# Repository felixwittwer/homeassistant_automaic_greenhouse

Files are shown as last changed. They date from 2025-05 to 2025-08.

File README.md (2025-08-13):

 &nbsp; &nbsp; 



<br>
<p align="center">
    
</p>
<br>

# homeassistant_automaic_greenhouse
A cool Project to make your greenhouse smart. What about automaic irrigation and collecting enviromental data right from your garden.

<p align="center">
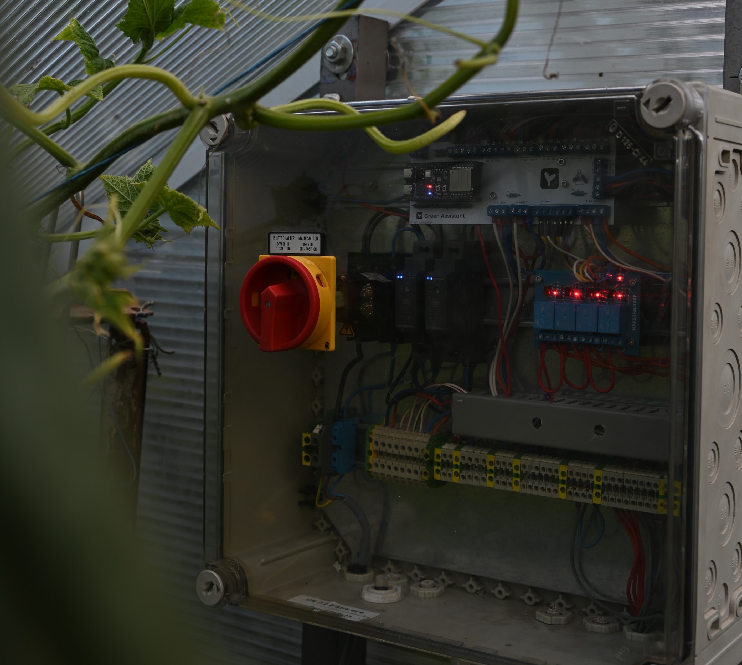
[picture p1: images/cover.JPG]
  
</p>

## About the project
This project actually is sthe second iteration on me trying to automate our greenhouse. The first version relied on an Arduino Uno powered by a 24V powertool battery and sensordata was logged to an SD-card. Since we now have power and wifi connectivity to the greenhouse I wanted to step up the game and build something that is way smarter and will hopefully last forever. If you were wondering this is why an industrial grade electrical box with rails was used.

## The concept of sensor and action modules
This project is a very specked out version of a greenhouse automation and environmental monitoring system. Due to cost or other reasons you might not include all the sensors used by me. To make it easyer to do so each sensor is getting his own folder inside the sensor modules directory. You will find everything you need to know about a so called sensor module inside this folder from CAD files, STL Files for 3D printing and scematics to instructions on sourcing the parts.

A detailed list of all sensors used in the project can be found in the [**sensor modules**](/sensor%20modules/) directory.

Like the sensors you might choose to leave out some action modules aka the parts that actually do something like the relais and solanoids for an irrigation system.

These so called action modules with all their corresponding documentation and files can be found in the [**action modules**](/action%20modules/) directory.

## Where to start

If you are completly new to this project you might take a look at the folowing map. Go thrugh the individual questions and build your own Green Assistant. Follow the link below to get to an interactive pdf version. Clicking on the links will be more func than searching in this Repo.

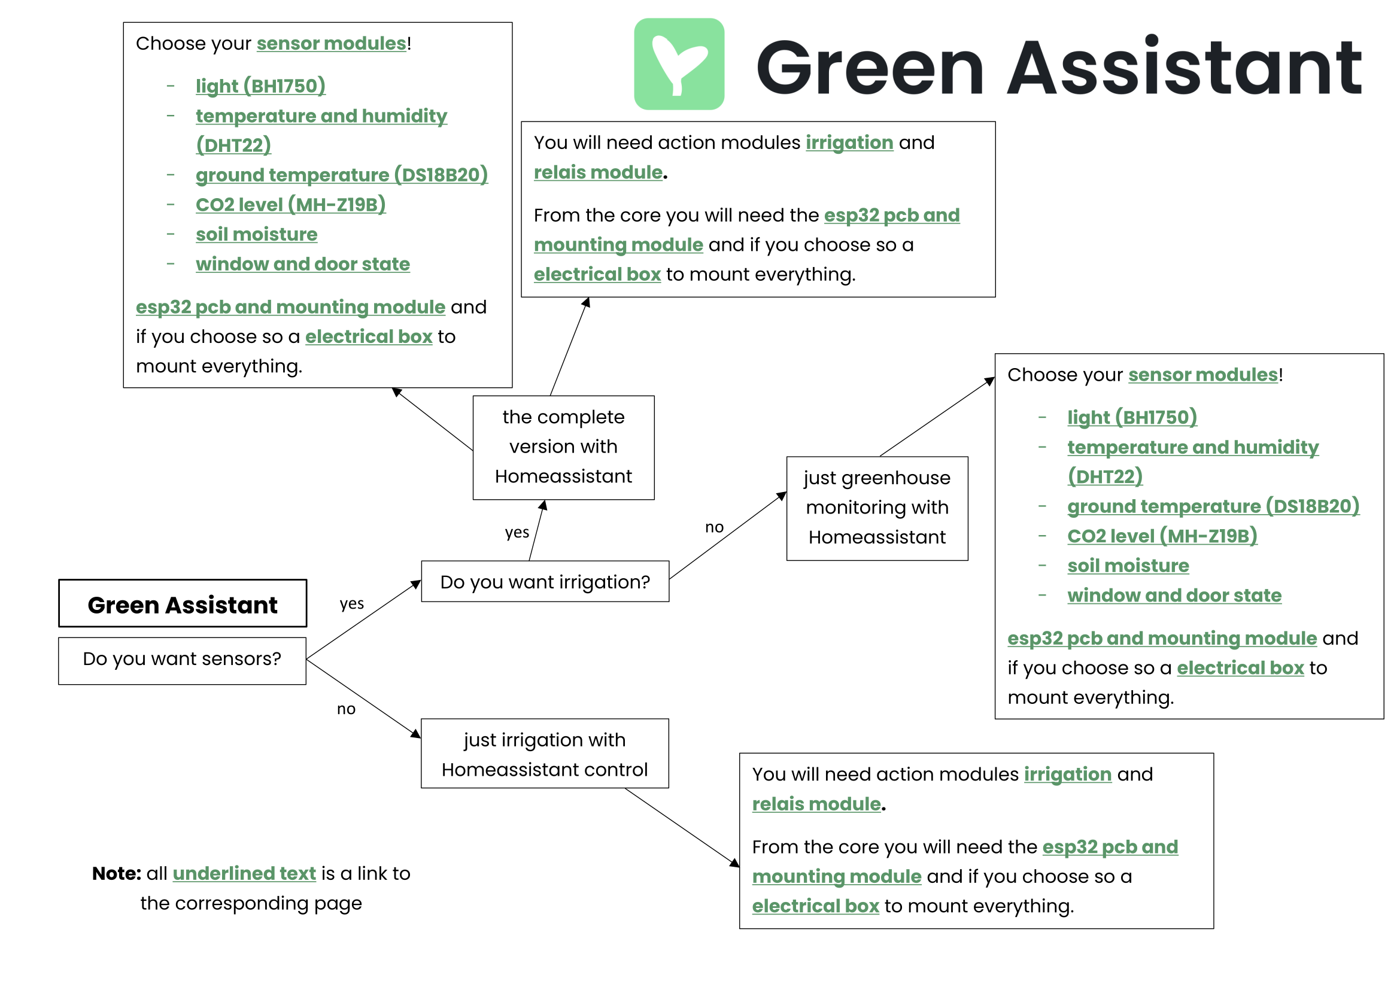
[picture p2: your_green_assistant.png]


<!-- ![Interactive PDF version](./your_green_assistant.pdf) -->

## The project

A list of all uesd parts can be found in the **parts** directory.

All files corresponding to the main part of the project so the electrical box with all the controll electronics can be found in the **core** directory.

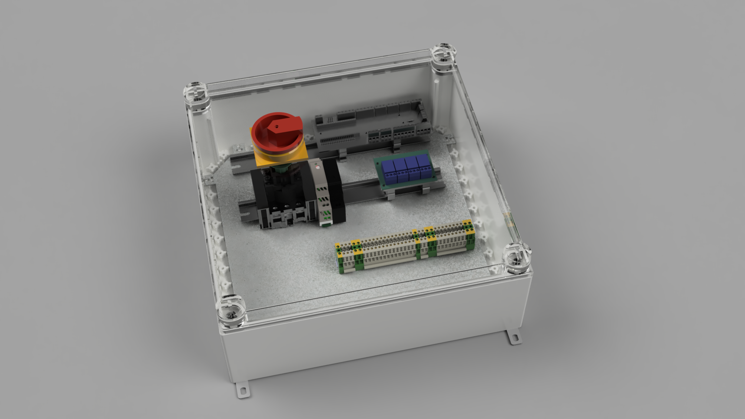
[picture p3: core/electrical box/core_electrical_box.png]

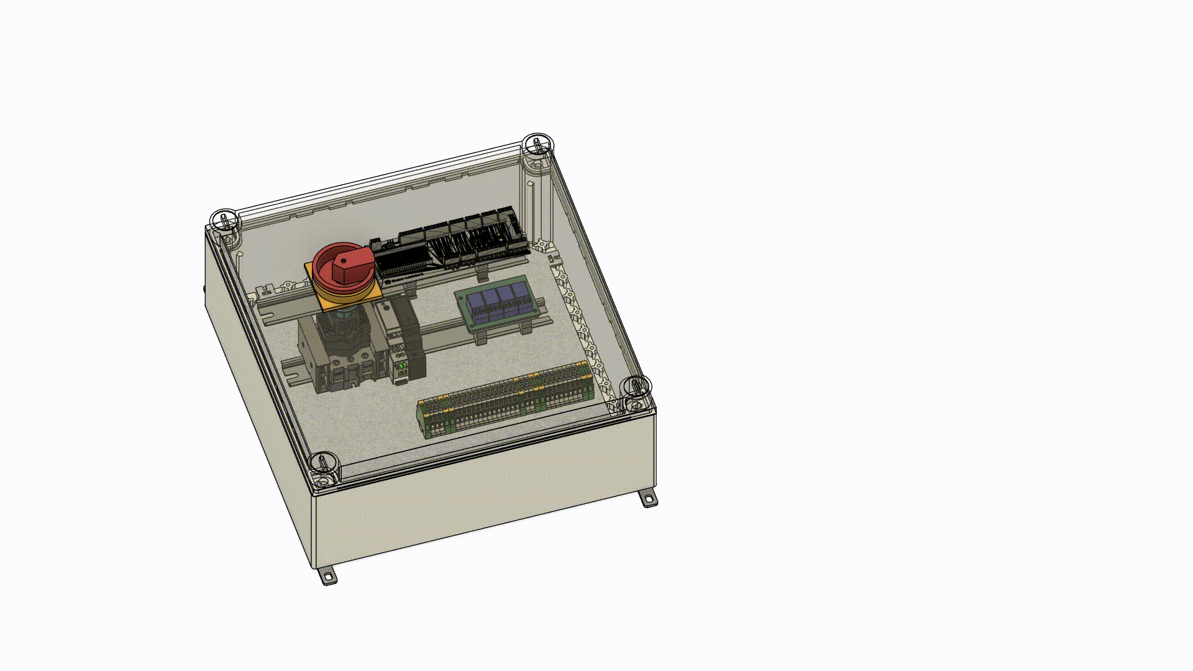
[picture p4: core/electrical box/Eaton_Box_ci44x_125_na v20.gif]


### Mounting hardware

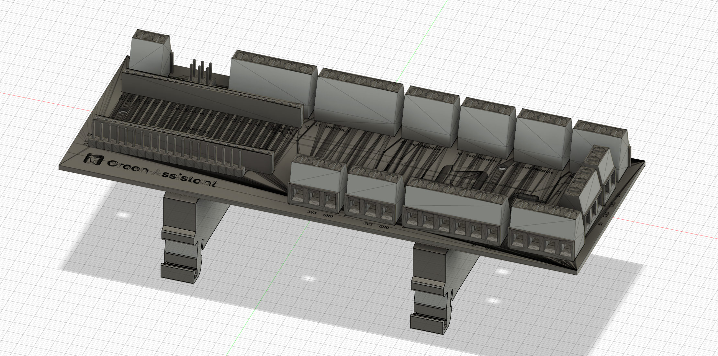
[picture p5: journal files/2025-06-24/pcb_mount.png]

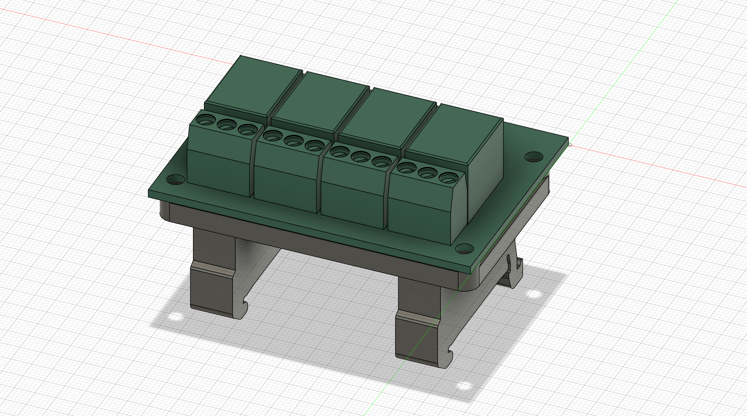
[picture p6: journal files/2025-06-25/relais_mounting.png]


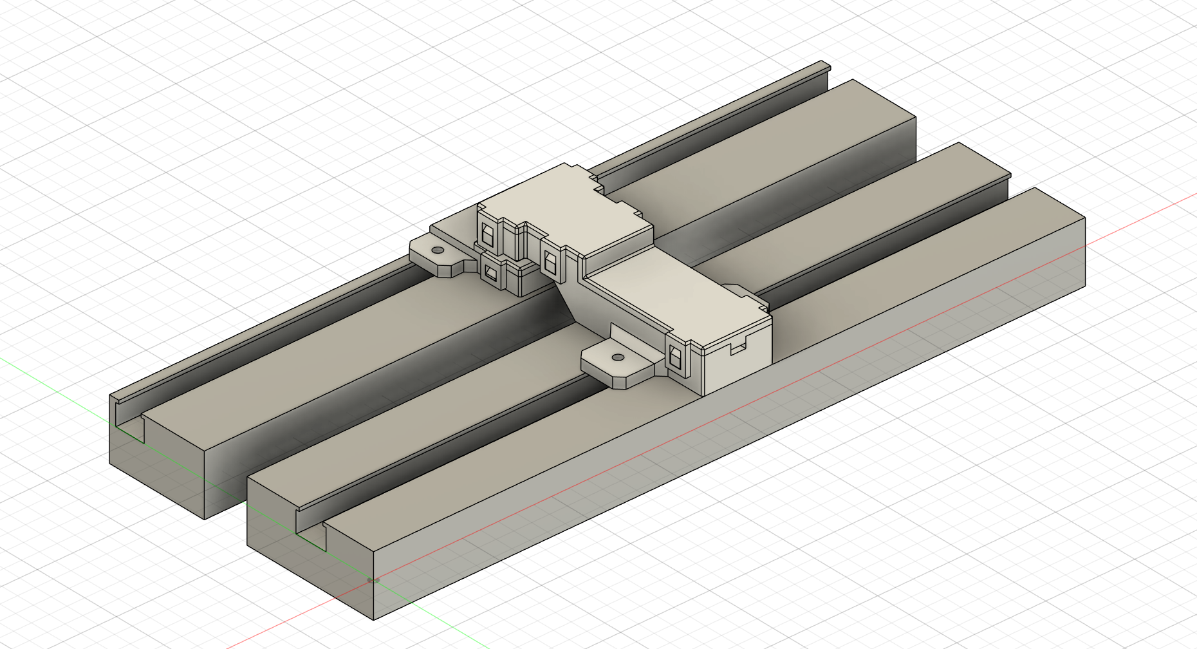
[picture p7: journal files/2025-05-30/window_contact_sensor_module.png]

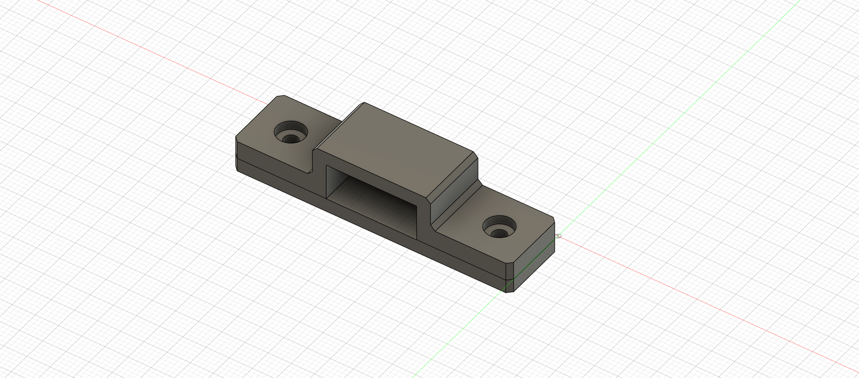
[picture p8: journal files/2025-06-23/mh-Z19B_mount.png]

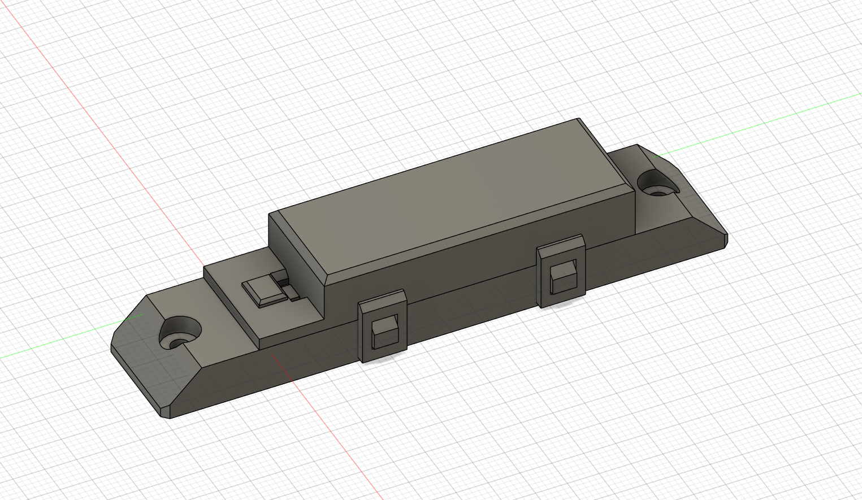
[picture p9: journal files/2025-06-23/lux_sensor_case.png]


### Irrigation system

<p float="left">
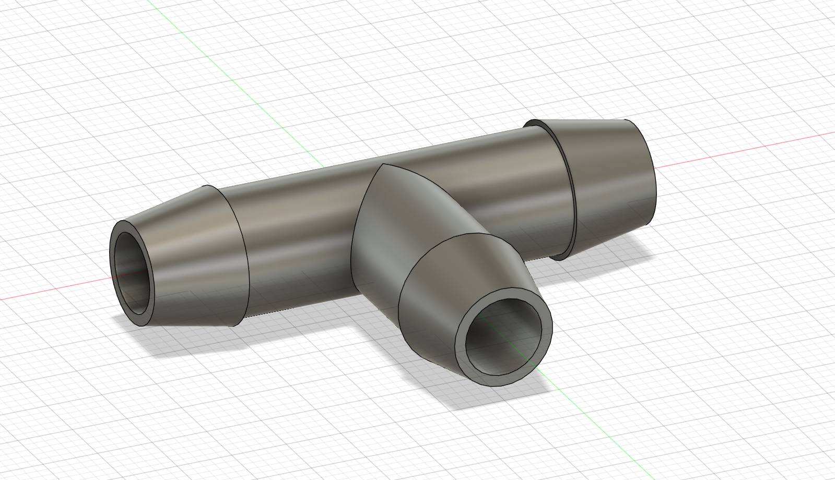
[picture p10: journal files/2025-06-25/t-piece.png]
  
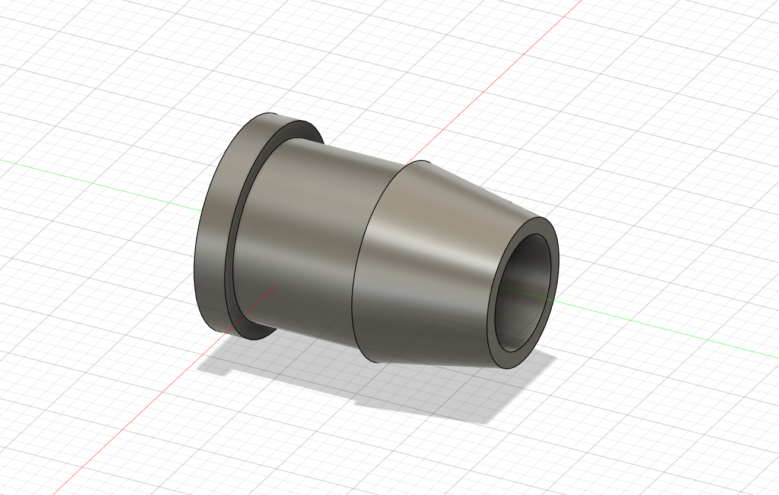
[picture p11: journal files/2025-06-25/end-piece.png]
  
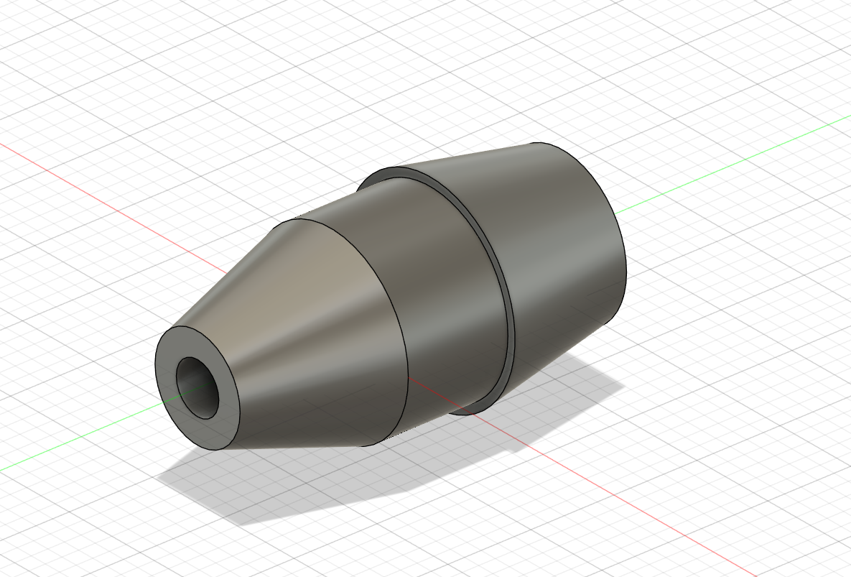
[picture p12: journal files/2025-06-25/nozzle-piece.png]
  
</p>

### PCB

You will need this PCB to connect all sensors reliably to the ESP32 S3. All unused pins of the ESP also have a connection to a pinheader so feel free to add sensors without needing to modify the PCB. 

PCB Sourcefiles can be found inside [core/esp32 pcb and mounting/pcb files/esp shield](./core/esp32%20pcb%20and%20mounting/pcb%20files/esp_shield/).

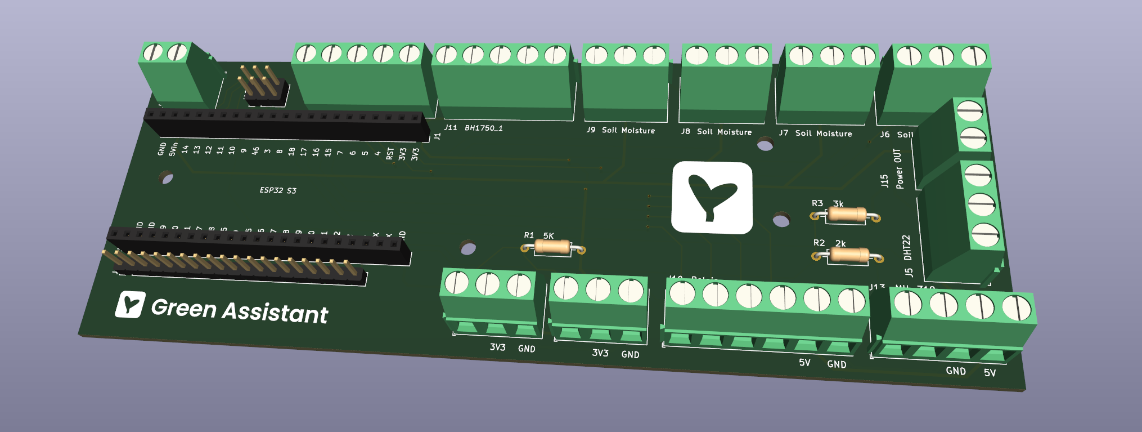
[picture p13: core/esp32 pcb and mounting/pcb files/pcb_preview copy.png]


<p float="left">
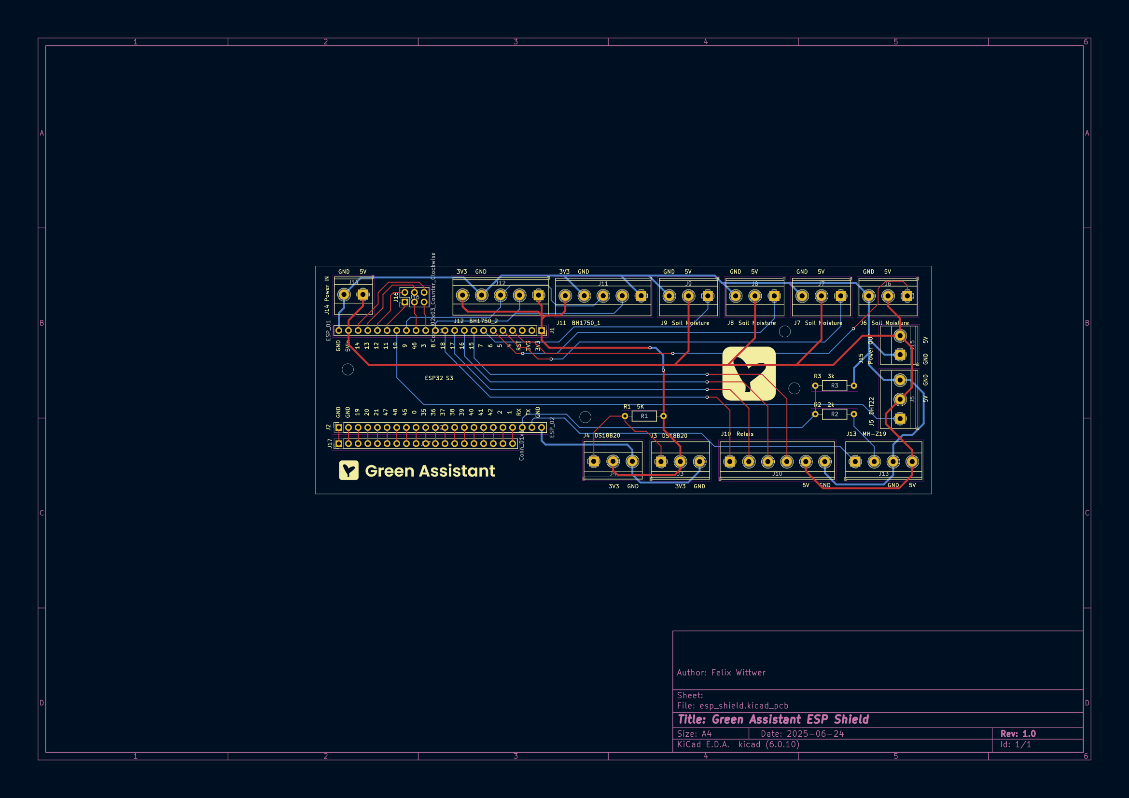
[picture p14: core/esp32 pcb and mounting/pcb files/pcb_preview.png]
  
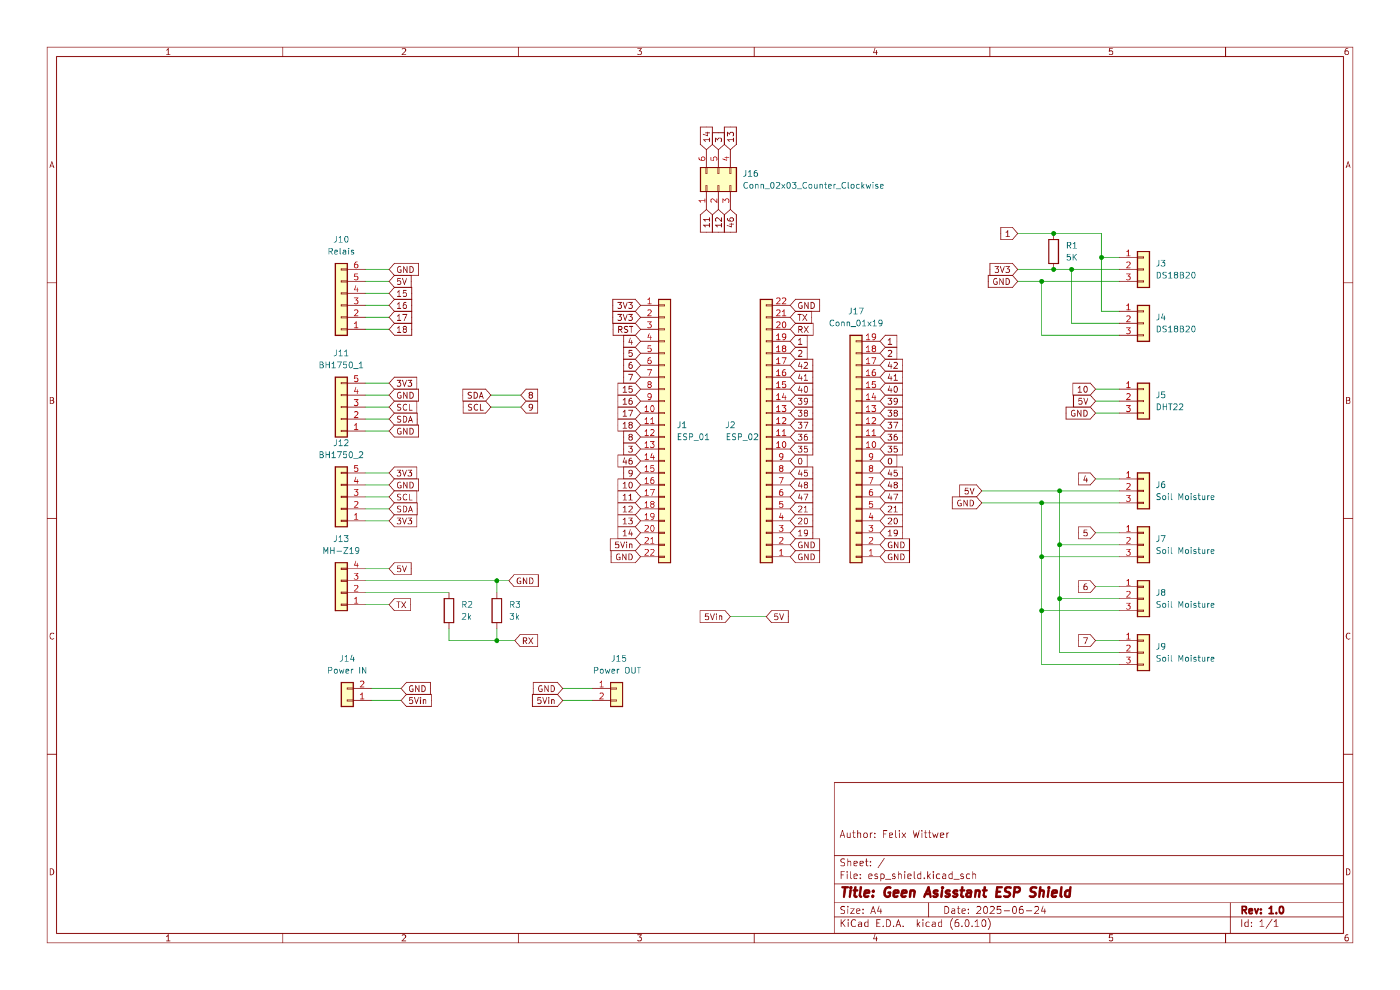
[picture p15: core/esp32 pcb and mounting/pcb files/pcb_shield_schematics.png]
  
</p>

### Wiring

When you have choosen your parts and want to build your Green Assistant have alook at this wiring diagramm of all the sensors.

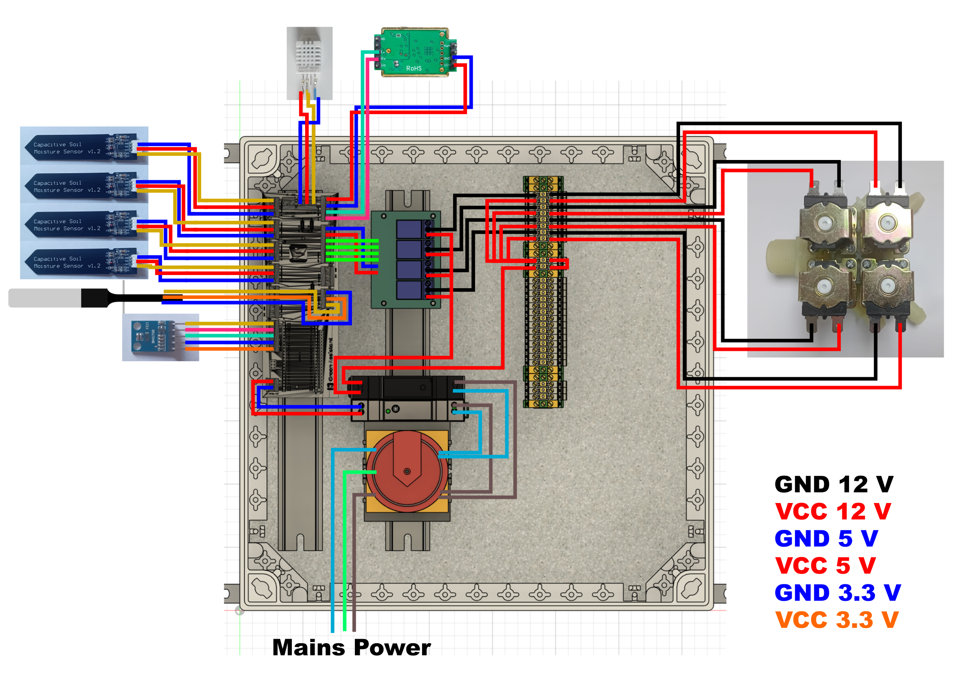
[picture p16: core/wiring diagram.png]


### Homeassistant Configuration and Dashboards

All stuff regarding Homeassistant can be found in the **homeassistant files** directory. Dashboards will be in a seperate folder.

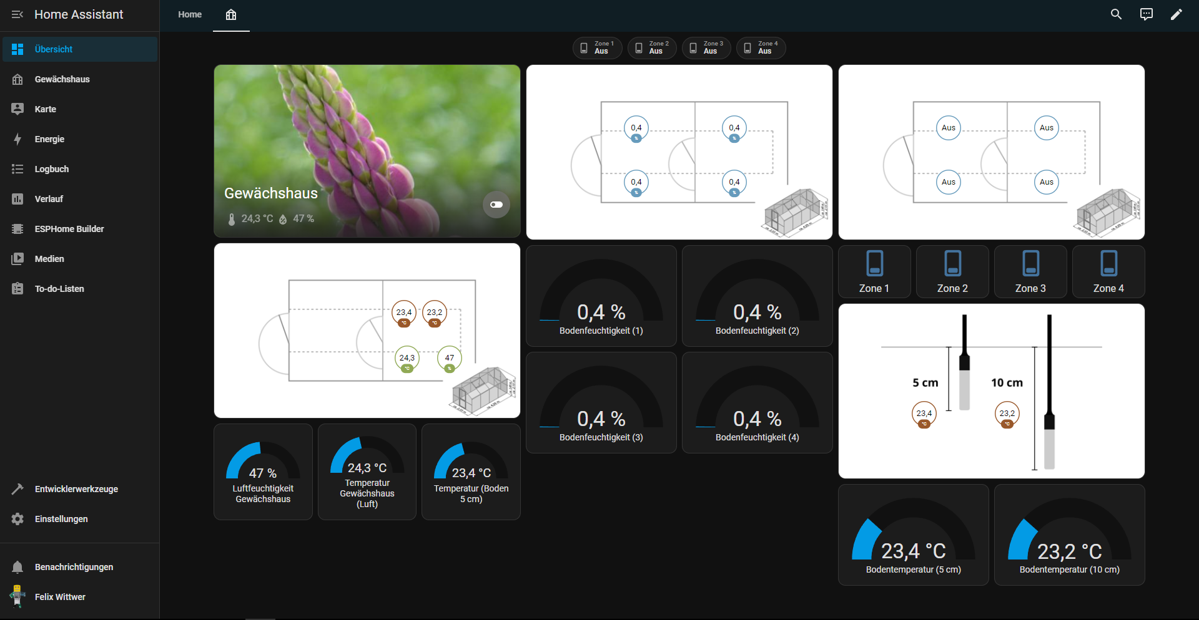
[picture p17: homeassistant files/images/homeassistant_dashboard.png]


<br>

### Project Video

https://youtu.be/dZTHF3ozego

# BOM

**@Hackclub** please note that some parts are a bit expensive but I already have them so they are listed here just for reference if somebody wontas to build his own Green Assistant. Go [here](./parts/Hackclub_BOM.csv) for a list of parts I seek Hackclub sponsorship for.

**sum: 318.49 USD**

**hopefully paid for by Hackclub :): 81.47 USD**

| part name | amount | price | link | note |
| --- | --- | ----- | ---- | ---  |
| 4 in 1 solanoid 12V DC | 1 | 17.46 USD | https://de.aliexpress.com/item/1005003222372894.html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
| 25m tubing 10mm inner diameter | 1 | 26.92 USD |https://de.aliexpress.com/item/1005006851012150.html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|
| Relais modul 4 Way | 1 | 1.19 USD | https://de.aliexpress.com/item/1005002867727977.html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
| Electrical box | 1 | 127.75 USD| https://www.elektro4000.de/Elektroinstallations-Systeme/Installationsverteiler/Leergehaeuse/Eaton-Unterkasten-U-CI44E::55531.html |any box or mounting with DIN Rails will be fine |
| Electrical Box Lid | 1 | 82.50 USD | https://www.elektro4000.de/Installationsmaterial/Verbindungsmaterial/Deckel/Gehaeuse-fuer-Montage-auf-der-Wand/Eaton-CI-Gehaeuse-Deckel-D125-CI44::55551.html
| DIN Rail Powersuply 5V DC Out 15W | 1 | 1.19 USD | https://de.aliexpress.com/item/1005006112378832.html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
| DIN Rail Powersuply 12V DC Out 15W | 1 | 1.19 USD | https://de.aliexpress.com/item/1005006112378832.html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
| ESP32-S3 | 1 | 1.19 USD | https://de.aliexpress.com/item/1005005051294262.html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 | |
| BH1750 Breakout | 1 | ~0.73 USD | https://de.aliexpress.com/item/1005007347385714.html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  | |
| DHT22 | 1 | ~0.94 USD | https://de.aliexpress.com/item/1005006963999579.html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  | --- |
| DS18B20 2 meter cable | 1 | ~1.17 USD | https://de.aliexpress.com/item/1005008024174225.html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  | --- |
| MH-Z19B | 1 | ~21.68 USD | https://de.aliexpress.com/item/4001296615950.html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  | --- |
| Capaciative Soil Moisture Sensor | 5 | ~2.37 USD (5pcs) | https://de.aliexpress.com/item/1005005202930632.html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  | --- |
| Shrink tubing 4:1 24mmx1.22 meter | 1 | ~3.08 USD | https://de.aliexpress.com/item/32812574636.html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  | --- |
| Reed switch Breackout | 1 | ~0.65 USD (10pcs) | https://de.aliexpress.com/item/1005008372135180.html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  | --- |
| magnet 10x2mm | 2 | ~2.26 USD (20pcs) | https://de.aliexpress.com/item/1005009266299777.html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  | --- |
| PCB (without assembly) | 1 | ~5 USD subject to JLCPCB | | if you choose assembly it will be more expensive but I already have the parts at home |
| M3 screws 10mm  | 8 | ~ | | --- |
| M3 screws 15mm  | 2 | ~ | | --- |
| M3 nuts | 10 | ~ | | --- |
| -> set of screws and nuts | 1| 1.19 USD | https://de.aliexpress.com/item/1005007273134914.html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
| some wire (15m) | 2 | 21.22 USD | https://de.aliexpress.com/item/1005007371239057.html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  | ethernet cable is shielded -> better for analog sensors (especially for longer distances) |
| t-piece | 22 | --- || 3D-printed part |
| nozzle-piece | 22 | --- || 3D-printed part |
| end-piece | 4 | --- || 3D-printed part |
| Ralais module mounting | 1 | --- || 3D-printed part |
| PCB Mounting | 1 | --- || 3D-printed part | 
| BH1750 case top | 1 | --- | | 3D-printed part |
| BH1750 case bottom | 1 | --- | | 3D-printed part |
| MH-Z19B case top | 1 | --- | | 3D-printed part |
| MH-Z19B case bottom | 1 | --- | | 3D-printed part |
| magnet case top | 1 | --- | | 3D-printed part |
| magnet case bottom | 1 | --- | | 3D-printed part |
| reed case top | 1 | --- | | 3D-printed part |
| reed case bottom | 1 | --- | | 3D-printed part |

**sum: 318.49 USD**

**hopefully paid for by Hackclub :) : 81.47 USD** 

# LICENSE
This work is licensed under CC BY-NC-SA 4.0. 

To view a copy of this license, visit https://creativecommons.org/licenses/by-nc-sa/4.0/



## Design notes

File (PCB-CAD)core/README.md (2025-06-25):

# core 

This direcrory contains all the important core stuff.

## electrical box

Inside **electrical box** folder.



## esp shield

Inside **esp32 pcb and mounting** folder.




## relais board

Inside action modules directory.

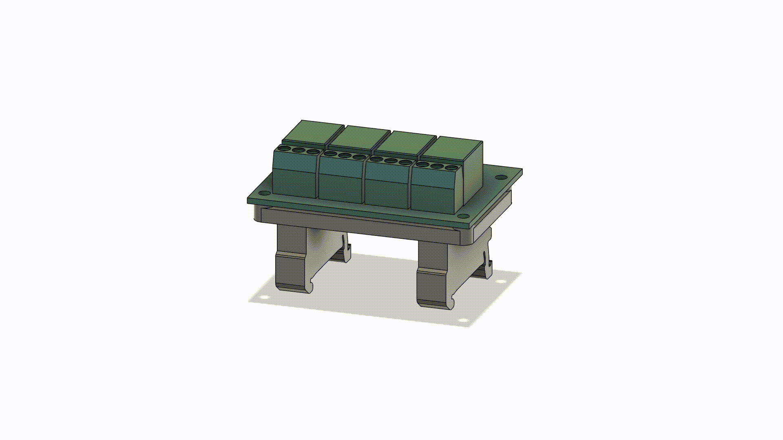
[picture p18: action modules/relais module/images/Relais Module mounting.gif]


## wiring diagram



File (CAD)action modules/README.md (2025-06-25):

#  action modules

This directory contains all files regarding the so called action modules.

## List of all action modules

| action module | folder name | needs extra PCB | needs case 3D printed | price  |
| --- | --- | --- | --- | --- |
| solanoids | irrigation | no | no | |
| relais | relais module | no | yes (rail mounting) | |

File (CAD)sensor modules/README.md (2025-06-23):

#  sensor modules

This directory contains all files regarding the so called sensor modules.

## List of all sensor modules

| sensor module | folder name | module task | needs extra PCB | needs case 3D printed | price (estimate may vary) |
| --- | --- | --- |--- | --- | --- |
| DHT22 | DHT22 | airtemperature and humidity | no | no | 3-5$ |
| DS18B20 | DS18B20 | ground temperature | no | no | 3-5$ |
| BH1750 | BH1750 | lux sensor (light) | no | yes | 3-5$ |
| soil moisture | soil moisture | soil moisture (capacitive)  | no | no | 5-7$ (four sensors) |
| MH-Z19B | MH-Z19B | CO2 level | no | yes | 23-25$ |
| window contacts | window contacts | window state | no | yes | 5-10$ (one contact) |
| door contact | window contatcs (in my case it works with my greenhouse) | door state | no | yes | 5-10$ (one contact) |

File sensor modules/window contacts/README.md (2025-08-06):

# window contacts

For sensing the state of the windows on the greenhouse reed switches and magnets will be used to build custom window contacts. When integrated in Homeassistant the window will only have two states: **opened/closed**. The contacts are specially designed for my greenhouse so you will probably need to adjust the files to your needs.

| part name | amount | price | | things you need |
| --- | --- | --- | - |--- |
| Reed switch Breackout | 1 | ~0.65 USD (10pcs) | https://de.aliexpress.com/item/1005008372135180.html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  | --- |
| M3 screws 15mm  | 4 | ~ | | --- |
| M3 nuts | 4 | ~ | | --- |
| some wire | 1 | ~ | | --- |
| magnet 10x2mm | 2 | ~2.26 USD (20pcs) | https://de.aliexpress.com/item/1005009266299777.html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  | --- |
| magnet case top | 1 | --- | | 3D printer |
| magnet case bottom | 1 | --- | | 3D printer |
| reed case top | 1 | --- | | 3D printer |
| reed case bottom | 1 | --- | | 3D printer |

[for screws and nuts have a visit you local hardware store or buy them in a larger pack]

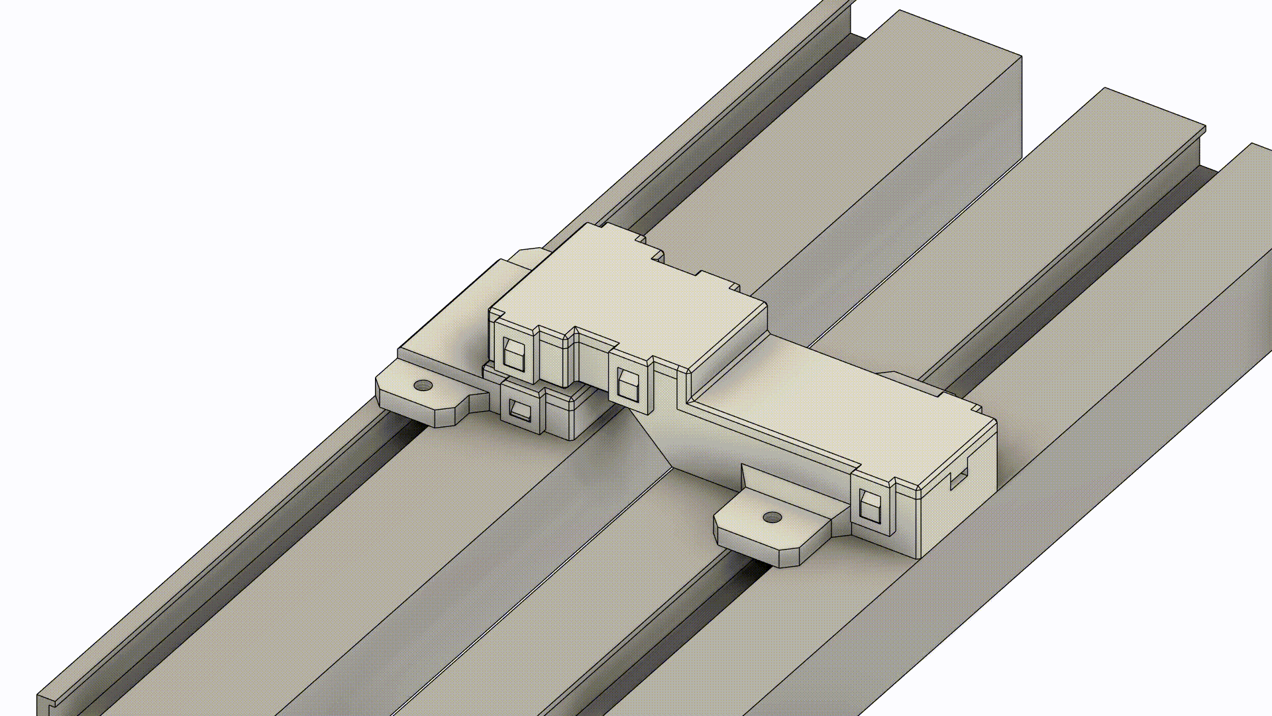
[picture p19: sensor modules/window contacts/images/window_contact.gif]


## 3D printing

The desing works totally fine with my SLA printer and Anycubig tough resin. You might need to think about placing your supports and material choices. The tough resin I use is a bit elastik so the clips dont snap of and can be bend temporarily during assembly.

Small note on that: there now actually is a second version that uses M3 screws for the sensor housing.

STL Files are inside this folder.

## ESPHome config

``` yaml
binary sensor:
  - platform: gpio
    pin: GPIOXX
    name: "window contact"
    device_class: window
    update_interval: 60s
```

for a door sensor:

``` yaml
binary sensor:
  - platform: gpio
    pin: GPIOXX
    name: "door contact"
    device_class: door
    update_interval: 60s
```

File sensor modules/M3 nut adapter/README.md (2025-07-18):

# M3 nut adapter

Some greenhouse aluminium extrusions may have a slot for M5 or even bigger nuts so I designed an adaper with whom you can stil use all the existing sensor module designs and just print some adapters for your M3 nuts to fit into the slot.

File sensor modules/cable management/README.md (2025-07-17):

# cable management

This folder contains parts to manage your cables. Especially some clips to mound the cables to the aluminium extrusions of the greenhouse.

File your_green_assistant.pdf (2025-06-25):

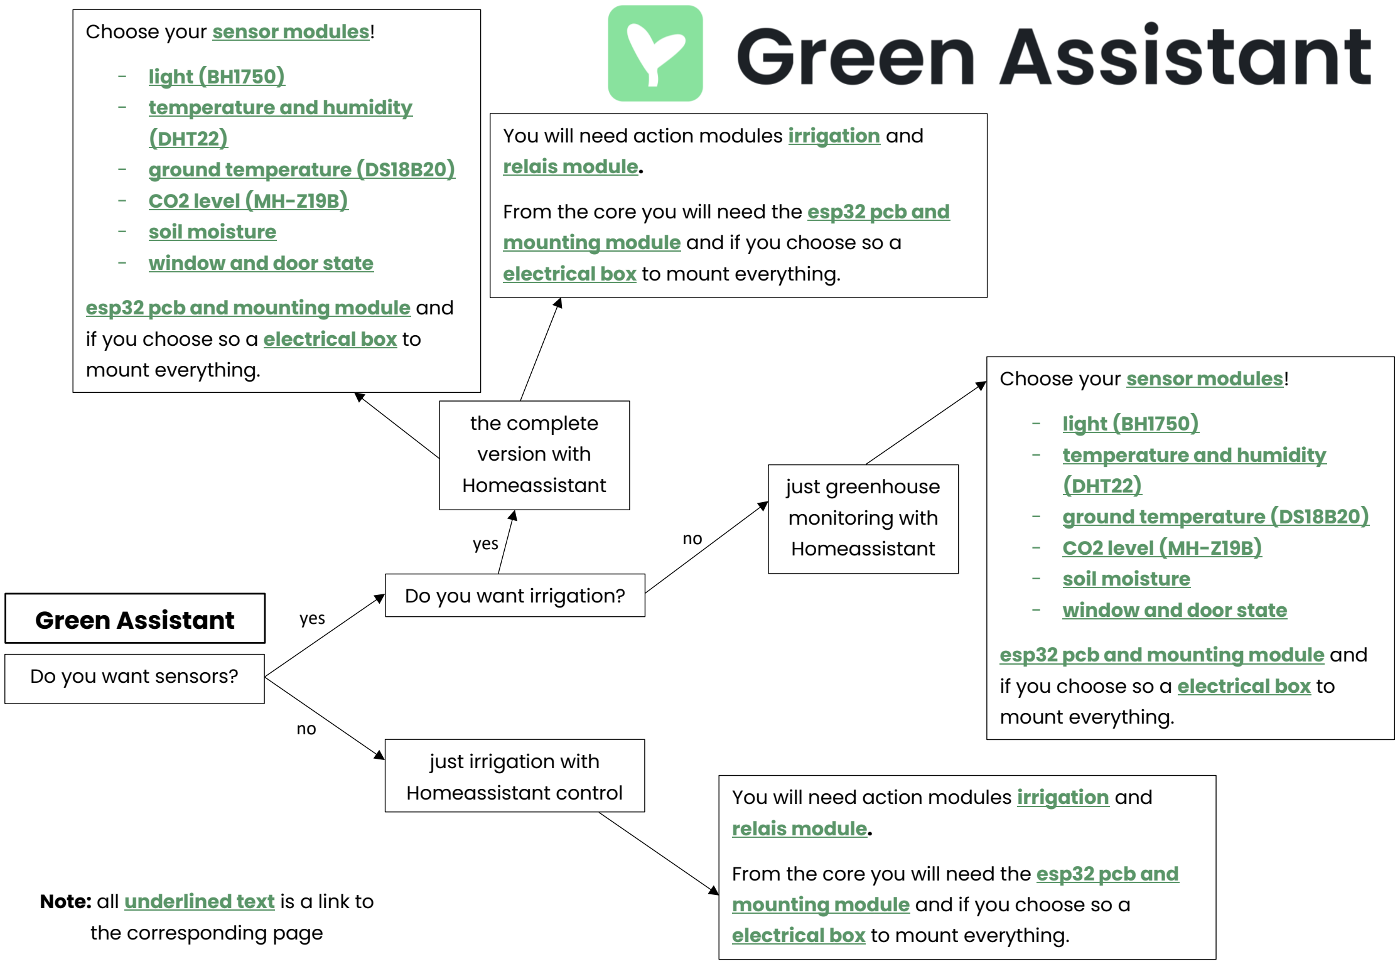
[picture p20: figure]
Green Assistant; Do you want sensors?; yes; just irrigation with; relais module.; mounting module and if you choose so a electrical box to mount everything.; Note: all underlined text is a link to the corresponding page; Do you want irrigation?; just greenhouse monitoring with Homeassistant; Choose your sensor modules!; - light (BH1750) - temperature and humidity (DHT22) - ground temperature (DS18B20) - CO2 level (MH-Z19B) - soil moisture - window and door state; esp32 pcb and mounting module and if you choose so a electrical box to mount everything.; the complete version with Homeassistant

Homeassistant control | You will need action modules irrigation (https://github.com/felixwittwer/homeassistant_automaic_greenhouse/tree/main/action%20modules/irrigation) and
| From the core you will need the esp32 pcb and

You will need action modules irrigation (https://github.com/felixwittwer/homeassistant_automaic_greenhouse/tree/main/action%20modules/irrigation) and

From the core you will need the esp32 pcb and

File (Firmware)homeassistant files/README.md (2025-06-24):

# Homeassistant files

This directory contains all files regarding Homeassistant.

## Homeassistand dashboards



## ESPHome configuration

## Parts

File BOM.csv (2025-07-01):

part name | quantity | price | link | notes
4 in 1 solanoid 12V DC | 1 | 17.46 USD | https://de.aliexpress.com/item/1005003222372894.html?pdp_ext_f={"order"%3A"90"%2C"eval"%3A"1"}&utparam-url=scene%3Asearch|query_from%3A
25m tubing 10mm inner diameter | 1 | 26.92 USD | https://de.aliexpress.com/item/1005006851012150.html?pdp_ext_f={"order"%3A"4"%2C"eval"%3A"1"}&utparam-url=scene%3Asearch|query_from%3A
Relais modul 4 Way | 1 | 1.19 USD | https://de.aliexpress.com/item/1005002867727977.html?pdp_ext_f={"order"%3A"2771"%2C"eval"%3A"1"}&utparam-url=scene%3Asearch|query_from%3A
Electrical box | 1 | 127.75 USD | https://www.elektro4000.de/Elektroinstallations-Systeme/Installationsverteiler/Leergehaeuse/Eaton-Unterkasten-U-CI44E::55531.html | any box or mounting with DIN Rails will be fine
Electrical Box Lid | 1 | 82.50 USD | https://www.elektro4000.de/Installationsmaterial/Verbindungsmaterial/Deckel/Gehaeuse-fuer-Montage-auf-der-Wand/Eaton-CI-Gehaeuse-Deckel-D125-CI44::55551.html
DIN Rail Powersuply 5V DC Out 15W | 1 | 1.19 USD | https://de.aliexpress.com/item/1005006112378832.html?pdp_ext_f={"order"%3A"1440"%2C"eval"%3A"1"}&utparam-url=scene%3Asearch|query_from%3A
DIN Rail Powersuply 12V DC Out 15W | 1 | 1.19 USD | https://de.aliexpress.com/item/1005006112378832.html?pdp_ext_f={"order"%3A"1440"%2C"eval"%3A"1"}&utparam-url=scene%3Asearch|query_from%3A
ESP32-S3 | 1 | 1.19 USD | https://de.aliexpress.com/item/1005005051294262.html?pdp_ext_f={"order"%3A"3124"%2C"eval"%3A"1"}&utparam-url=scene%3Asearch|query_from%3A
BH1750 Breakout | 1 | ~0.73 USD | https://de.aliexpress.com/item/1005007347385714.html?pdp_ext_f={"order"%3A"3"%2C"eval"%3A"1"}&utparam-url=scene%3Asearch|query_from%3A&gatewayAdapt=glo2deu
DHT22 | 1 | ~0.94 USD | https://de.aliexpress.com/item/1005006963999579.html?pdp_ext_f={"order"%3A"48"%2C"eval"%3A"1"}&utparam-url=scene%3Asearch|query_from%3A&search_p4p_id=202506230828074971261634829080000442240_2 | ---
DS18B20 2 meter cable | 1 | ~1.17 USD | https://de.aliexpress.com/item/1005008024174225.html?pdp_ext_f={"order"%3A"1023"%2C"eval"%3A"1"}&utparam-url=scene%3Asearch|query_from%3A | ---
MH-Z19B | 1 | ~21.68 USD | https://de.aliexpress.com/item/4001296615950.html?pdp_ext_f={"order"%3A"96"%2C"eval"%3A"1"}&utparam-url=scene%3Asearch|query_from%3A | ---
Capaciative Soil Moisture Sensor | 5 | ~2.37 USD (5pcs) | https://de.aliexpress.com/item/1005005202930632.html?pdp_ext_f={"order"%3A"2164"%2C"eval"%3A"1"}&utparam-url=scene%3Asearch|query_from%3A | ---
Shrink tubing 4:1 24mmx1.22 meter | 1 | ~3.08 USD | https://de.aliexpress.com/item/32812574636.html?pdp_ext_f={"order"%3A"1827"%2C"eval"%3A"1"}&utparam-url=scene%3Asearch|query_from%3A | ---
Reed switch Breackout | 1 | ~0.65 USD (10pcs) | https://de.aliexpress.com/item/1005008372135180.html?pdp_ext_f={"order"%3A"45"%2C"eval"%3A"1"}&utparam-url=scene%3Asearch|query_from%3A | ---
magnet 10x2mm | 2 | ~2.26 USD (20pcs) | https://de.aliexpress.com/item/1005009266299777.html?pdp_ext_f={"order"%3A"42"%2C"eval"%3A"1"}&utparam-url=scene%3Asearch|query_from%3A | ---
PCB (without assembly) | 1 | ~5 USD subject to JLCPCB |  | if you choose assembly it will be more expensive but I already have the parts at home
M3 screws 10mm | 8 | ~ |  | ---
M3 screws 15mm | 2 | ~ |  | ---
M3 nuts | 10 | ~ |  | ---
-> set of screws and nuts | 1 | 1.19 USD | https://de.aliexpress.com/item/1005007273134914.html?pdp_ext_f={"order"%3A"476"%2C"eval"%3A"1"}&utparam-url=scene%3Asearch|query_from%3A
some wire (15m) | 2 | 21.22 USD | https://de.aliexpress.com/item/1005007371239057.html?pdp_ext_f={"order"%3A"5"%2C"eval"%3A"1"}&utparam-url=scene%3Asearch|query_from%3A&search_p4p_id=2025063002162114202903362944350000136812_2 | ethernet cable is shielded -> better for analog sensors (especially for longer distances)
t-piece | 22 | --- |  | 3D-printed part
nozzle-piece | 22 | --- |  | 3D-printed part
end-piece | 4 | --- |  | 3D-printed part
Ralais module mounting | 1 | --- |  | 3D-printed part
PCB Mounting | 1 | --- |  | 3D-printed part
BH1750 case top | 1 | --- |  | 3D-printed part
BH1750 case bottom | 1 | --- |  | 3D-printed part
MH-Z19B case top | 1 | --- |  | 3D-printed part
MH-Z19B case bottom | 1 | --- |  | 3D-printed part
magnet case top | 1 | --- |  | 3D-printed part
magnet case bottom | 1 | --- |  | 3D-printed part
reed case top | 1 | --- |  | 3D-printed part
reed case bottom | 1 | --- |  | 3D-printed part
total |  | ~318.49 USD

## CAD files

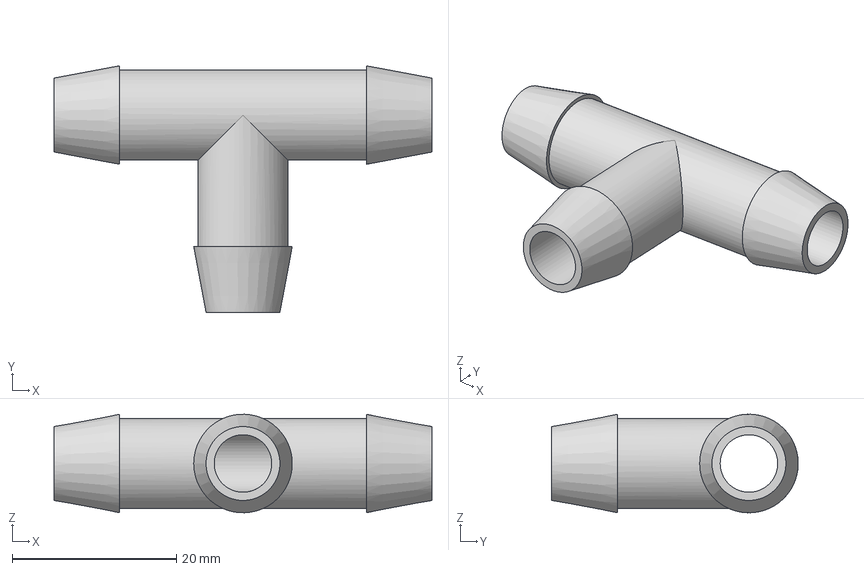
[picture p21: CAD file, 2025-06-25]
(CAD)action modules/irrigation/3D parts - tubing parts/t-piece.step
46.0 x 30.0 x 12.0 mm

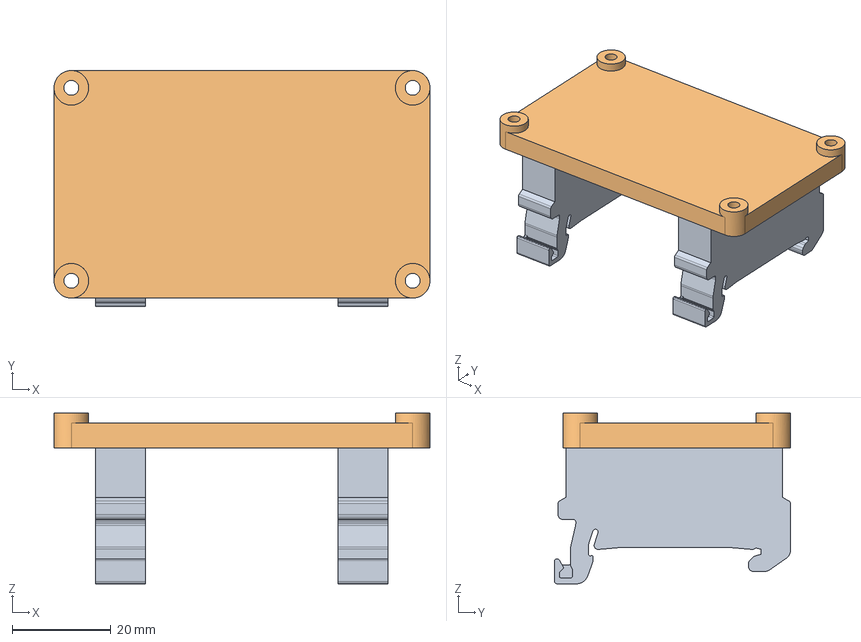
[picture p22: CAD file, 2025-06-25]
(CAD)action modules/relais module/mounting/Relais Module mounting.step
76.0 x 47.7 x 34.5 mm
SRK100ISO_2A_STEP x 2

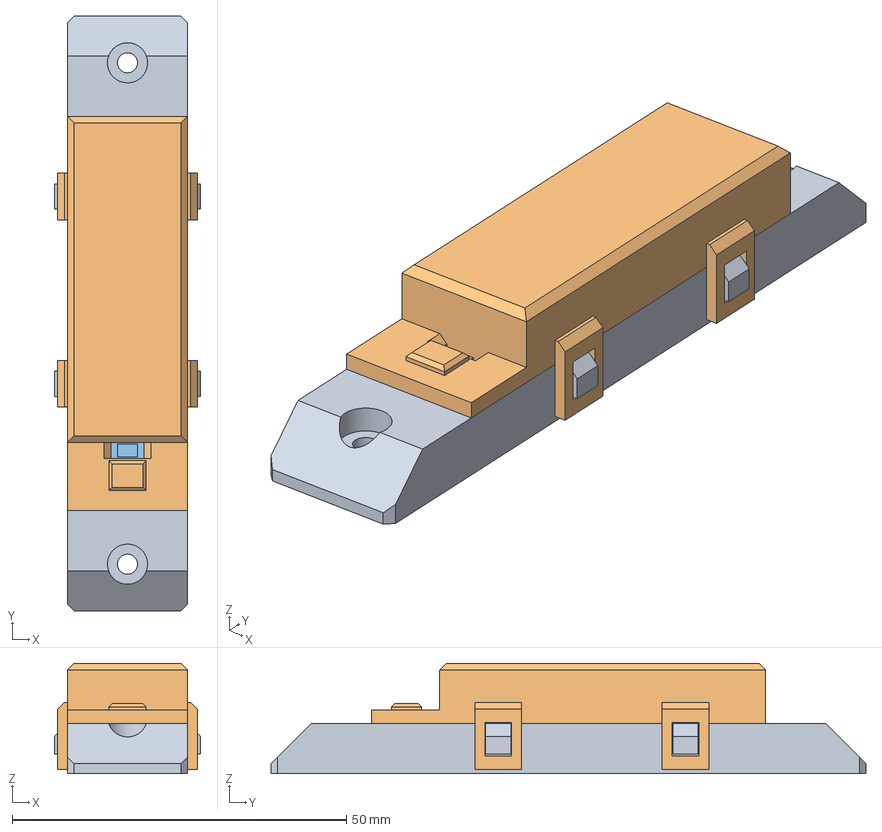
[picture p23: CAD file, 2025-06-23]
(CAD)sensor modules/BH1750/bh1750_case.step
21.9 x 89.0 x 16.5 mm
clip v2
clip v2 (1)
clip v2(Spiegeln)
clip v2(Spiegeln) (1)
Komponente9
Komponente10
sensor

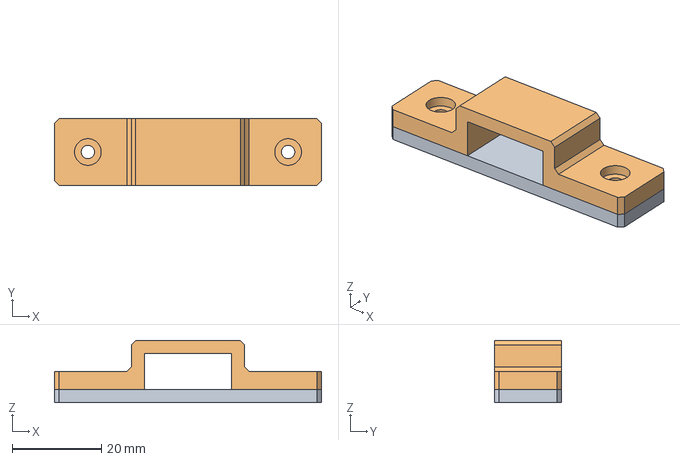
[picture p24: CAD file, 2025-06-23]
(CAD)sensor modules/MH-Z19B/MH-Z19B mount.step
60.0 x 15.0 x 14.0 mm
clamp bottom
clamp top

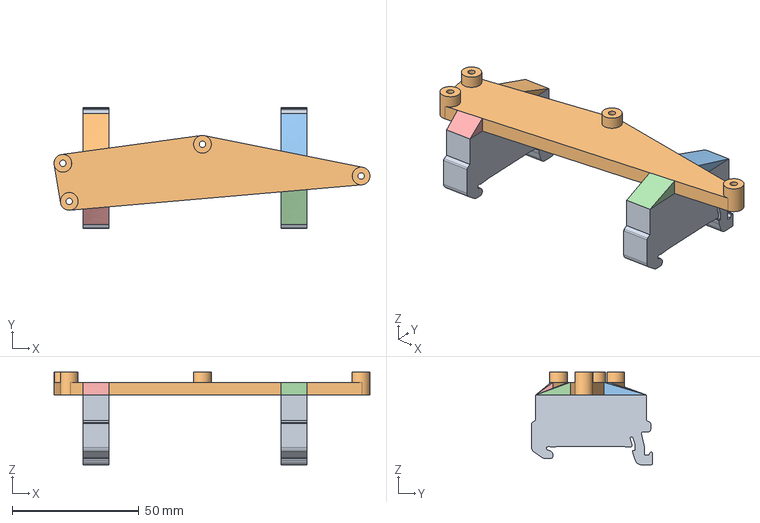
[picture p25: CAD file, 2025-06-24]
(PCB-CAD)core/esp32 pcb and mounting/mounting/pcb_mount.step
124.5 x 47.7 x 36.5 mm
SRK100ISO_2A_STEP x 2

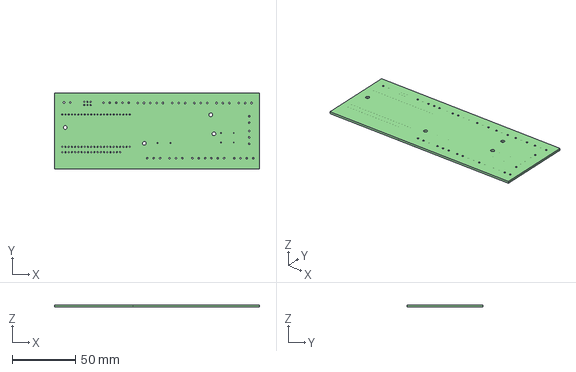
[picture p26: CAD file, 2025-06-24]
(PCB-CAD)core/esp32 pcb and mounting/pcb files/esp_shield/esp_shield.step
162.0 x 60.0 x 1.60 mm

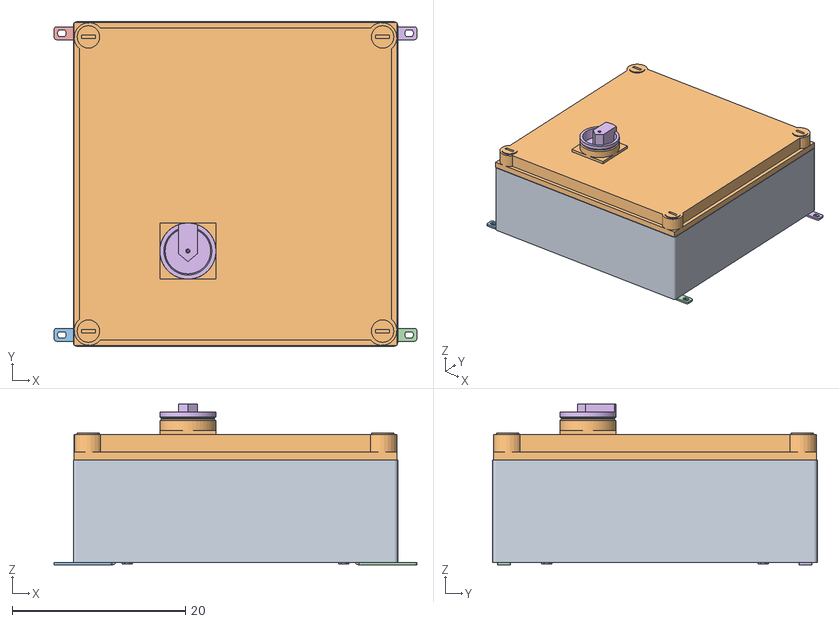
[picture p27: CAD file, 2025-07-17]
core/electrical box/core_electircal_box.obj
41.9 x 37.5 x 18.6
Körper1
Körper1:1
Körper1:2
Körper1:3
Körper1:4
Körper1:5
Körper1:6
Körper1:7
Körper1:8
Körper1:9
Körper1:10
Körper1:11
Körper1:12
Körper1:13
Körper1:14
Körper1:15
Körper1:16
Körper1:17
Körper1:18
Körper1:19
Körper1:20
Körper1:21
Körper1:22
Körper1:23
Körper1:24
Körper1:25
Körper1:26
Körper1:27
Körper1:28
Körper1:29
Körper1:30
Körper1:31
Körper1:32
Körper1:33

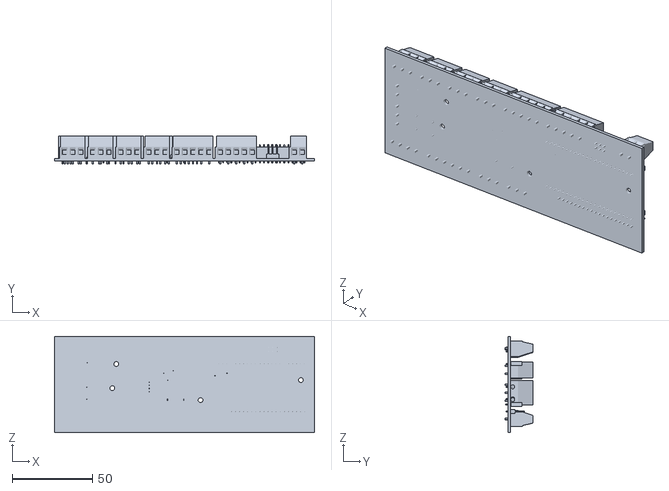
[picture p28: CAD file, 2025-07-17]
core/esp32 pcb and mounting/mounting/pcb.stl
162.0 x 17.3 x 60.0

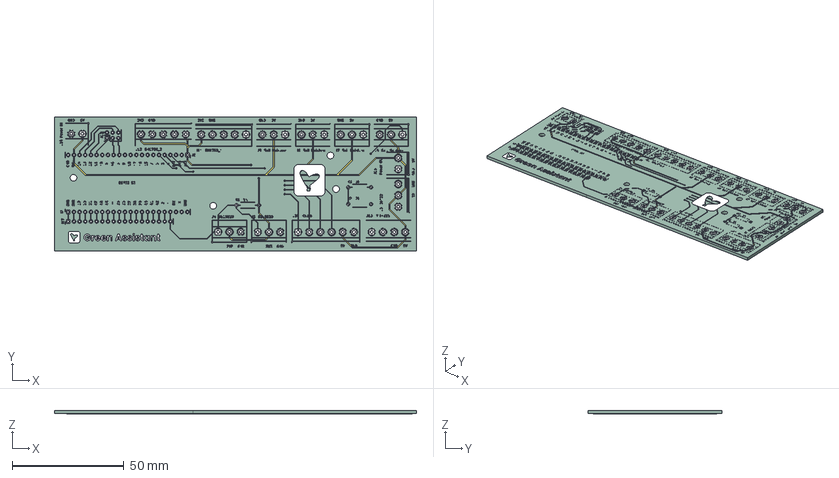
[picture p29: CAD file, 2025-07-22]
core/esp32 pcb and mounting/pcb files/esp_shield/esp_shield.step
162.0 x 60.0 x 1.62 mm
esp_shield_copper
esp_shield_pad
esp_shield_via
esp_shield_silkscreen
esp_shield_PCB

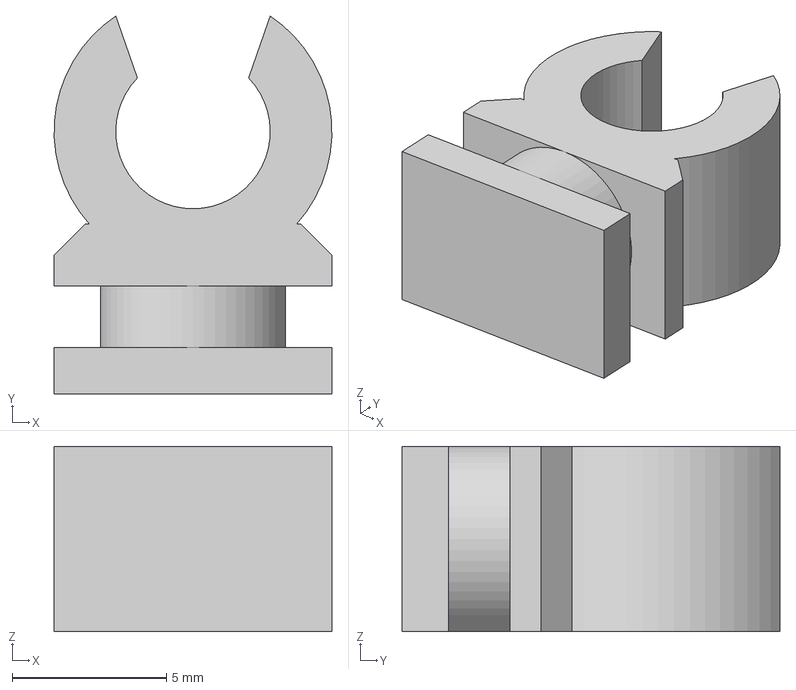
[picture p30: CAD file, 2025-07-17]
sensor modules/cable management/cable_clip.step
9.00 x 12.2 x 6.00 mm

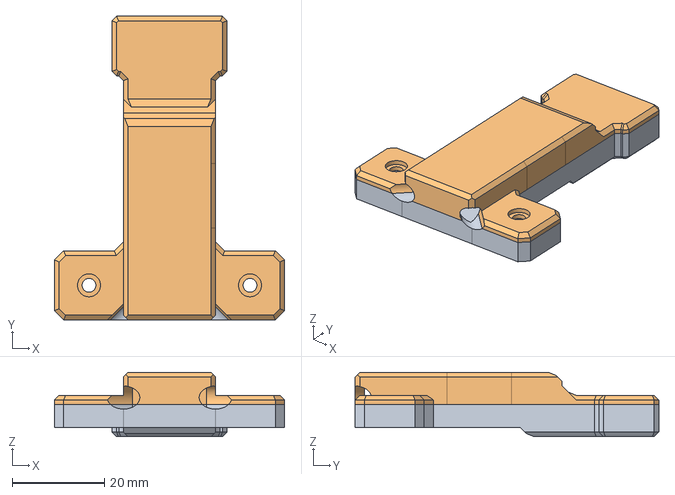
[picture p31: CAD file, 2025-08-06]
sensor modules/door contact/new_door_sensor.step
50.0 x 66.0 x 14.0 mm

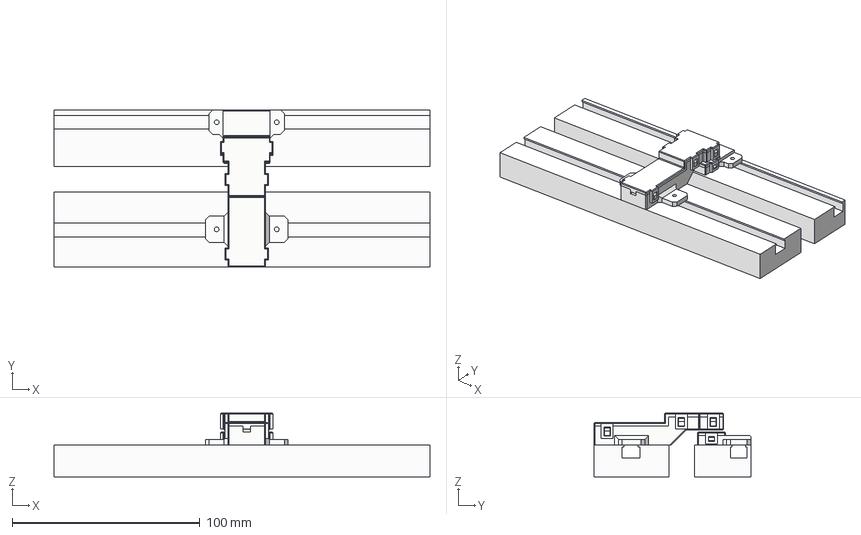
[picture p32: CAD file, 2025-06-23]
sensor modules/window contacts/clip_edition/window_contacts.step
200.0 x 83.5 x 34.0 mm
Unten
Oben
Unten_1
Oben_1

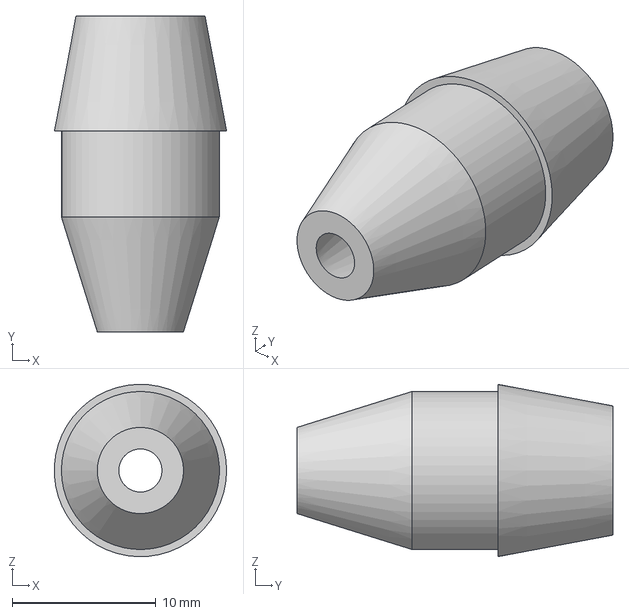
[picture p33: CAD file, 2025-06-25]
(CAD)action modules/irrigation/3D parts - tubing parts/nozzle-piece.step
12.0 x 22.0 x 12.0 mm

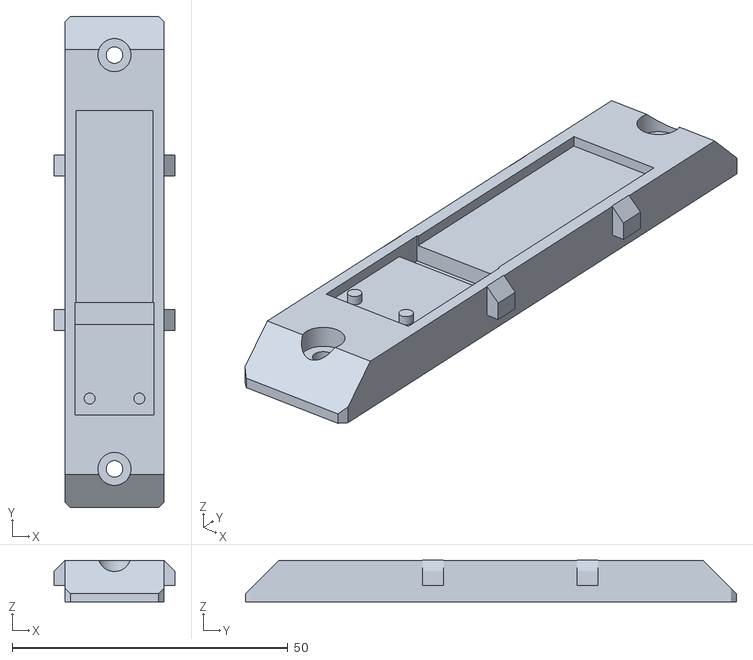
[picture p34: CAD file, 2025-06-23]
(CAD)sensor modules/BH1750/bh1750_bottom.stl
21.9 x 89.0 x 7.55

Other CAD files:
(CAD)sensor modules/MH-Z19B/MH-Z19B mount top.stl
core/electrical box/Eaton_Box_ci44x_125_na v20.step
sensor modules/door contact/door_magnet_holder.step
(CAD)action modules/irrigation/3D parts - tubing parts/end-piece.stl
(CAD)action modules/irrigation/3D parts - tubing parts/nozzle-piece.stl
(CAD)action modules/irrigation/3D parts - tubing parts/t-piece.stl
(CAD)action modules/relais module/mounting/Relais Module mounting.3mf
(CAD)action modules/relais module/mounting/Relais Module mounting.stl
(CAD)sensor modules/BH1750/bh1750_top.stl
(CAD)sensor modules/MH-Z19B/MH-Z19B mount bottom.stl
(PCB-CAD)core/electrical box/Eaton_Box_ci44x_125_na v20.f3z
(PCB-CAD)core/electrical box/core_electircal_box.f3z
(PCB-CAD)core/esp32 pcb and mounting/mounting/pcb_mount.3mf
(PCB-CAD)core/esp32 pcb and mounting/mounting/pcb_mount.stl
action modules/irrigation/3D parts - tubing parts/end-piece.stl
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

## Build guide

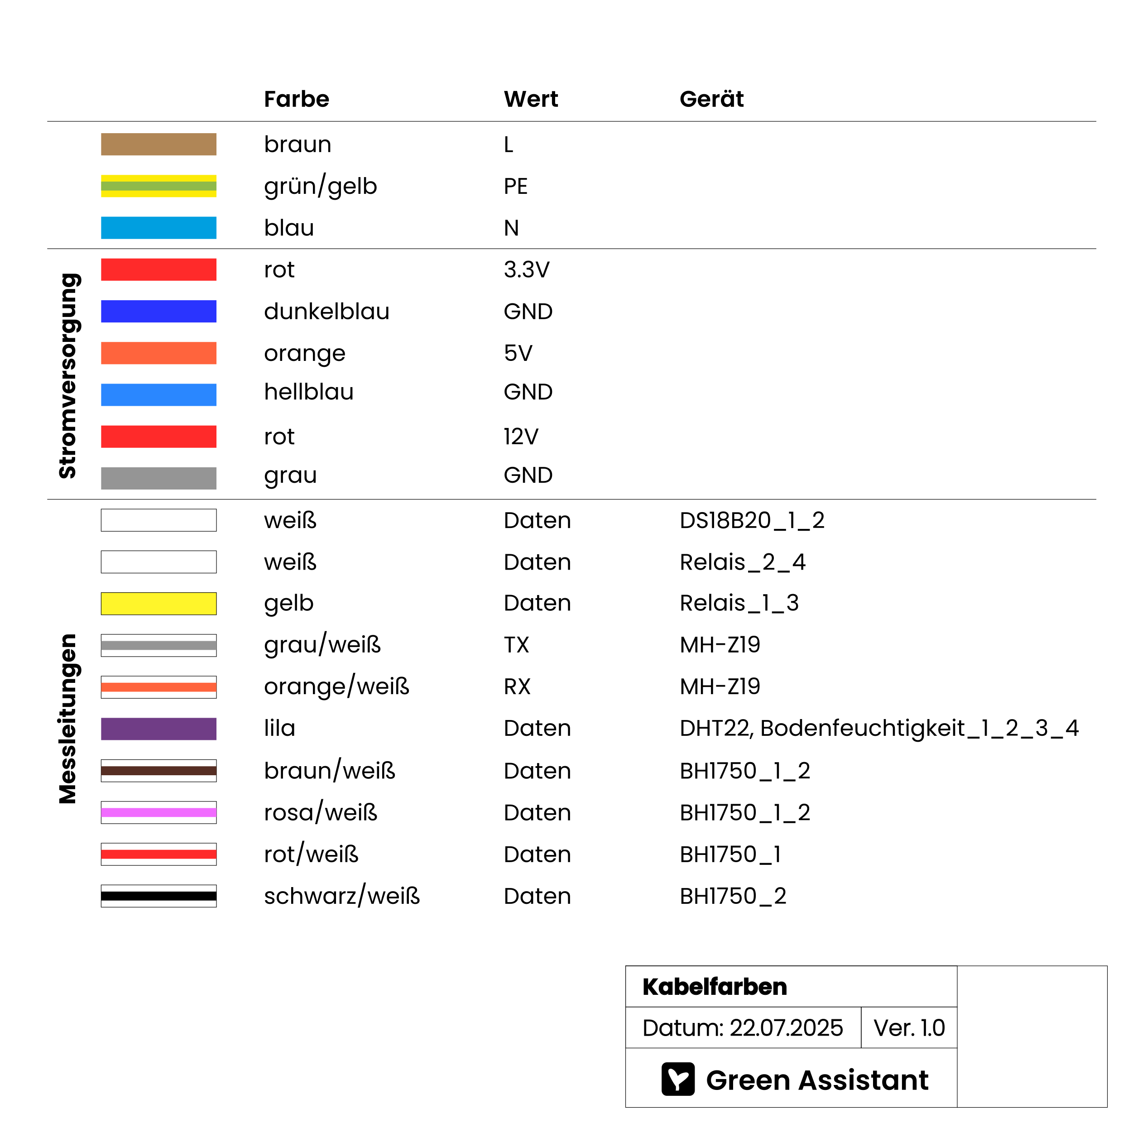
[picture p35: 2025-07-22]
core/manual/wiring_color.png

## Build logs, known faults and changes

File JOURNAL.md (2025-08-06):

---
title: "Homeassistant automatic greeenhouse"
author: "Felix Wittwer (fegolix)"
description: "Automatic greenhouse with Homeassistant integration."
created_at: "2024-03-25"
---

# Journal

Here you can see a documentation of the entire development process.

**Total hours spent: 80h**

## May 25th (30m): initial setup

Just setting up the Git Repo. Finding some cool badges for the README.md file. Doing some parst reasearch.





## May 29th (1h): start desingning core electrical box

Finding 3D Models for electrical box and other parts. It actually took some time to find a 3D model of the electrical Box I want to repurpose for the project. And because I am sometimes a lazy person [here its more about effectiveness; who needs to design a box when manufacturues profide the files :)] But from my experiente they like to hide them.

I eventually found the .stp files I was searching for and imported them into Fusion 360. Looks great and will defenitly better visualize the Idea and is perfect for planning.

<p float="left">
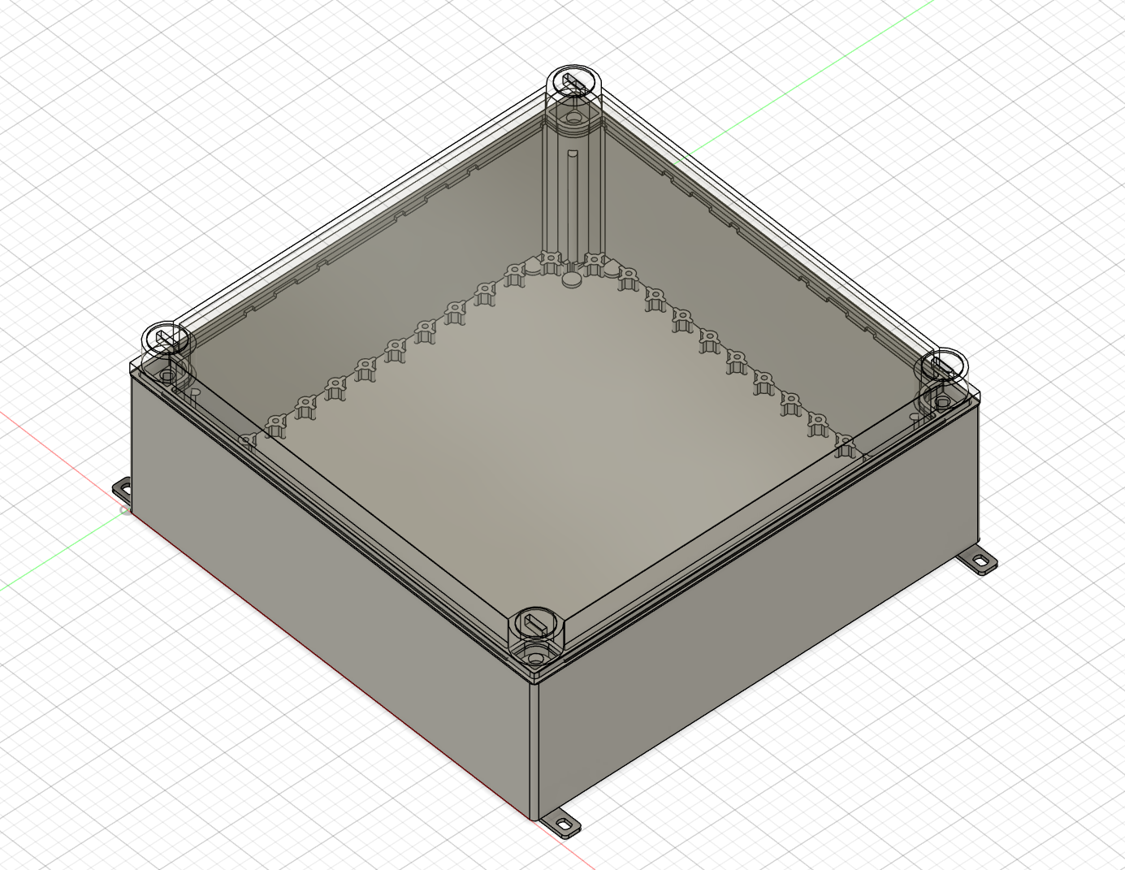
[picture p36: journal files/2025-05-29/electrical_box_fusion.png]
  
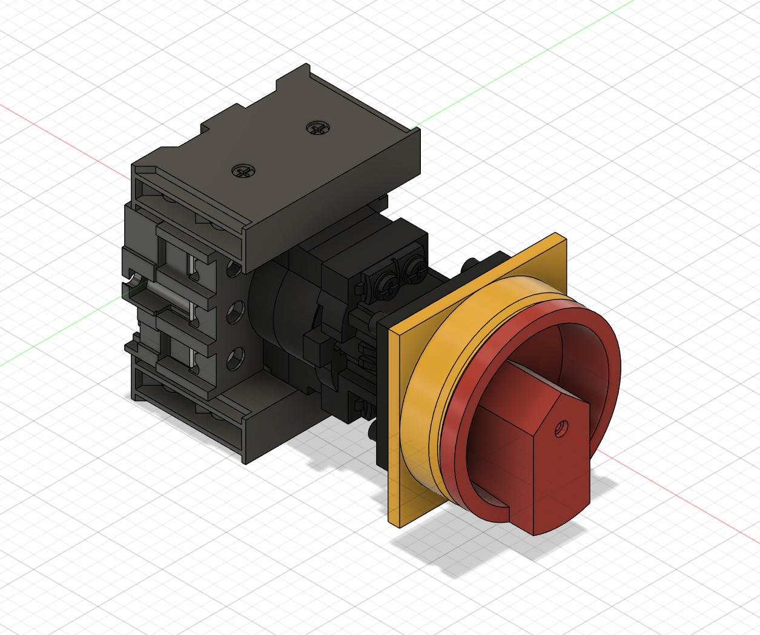
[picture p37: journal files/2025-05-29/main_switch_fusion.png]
  
</p>

## May 30th (7h 30m): configuring my electrical box

### Session 1 (1h 30m)

I just wrote some imortant stuff to the README and build a logical project structure. The README also explains the concept of sensor modules. The concept of sensor moduels I introduced makes it easy to adapt and adjust the project to you individual needs. I added a License fole just to be clear on how the project can be used in the future.

### Session 2 (2h 30m)

I modeled some parts on my own like the ground plate on the inside of the box where everything is mounted. Furthermore I added the main switch and DIN Rais inside the box with some terminals for the wires. I also decided on writing sub README files for the individual folders bacause Github can't display lager 3D files. Now there will be great renders right in every directory. 

<p float="left">
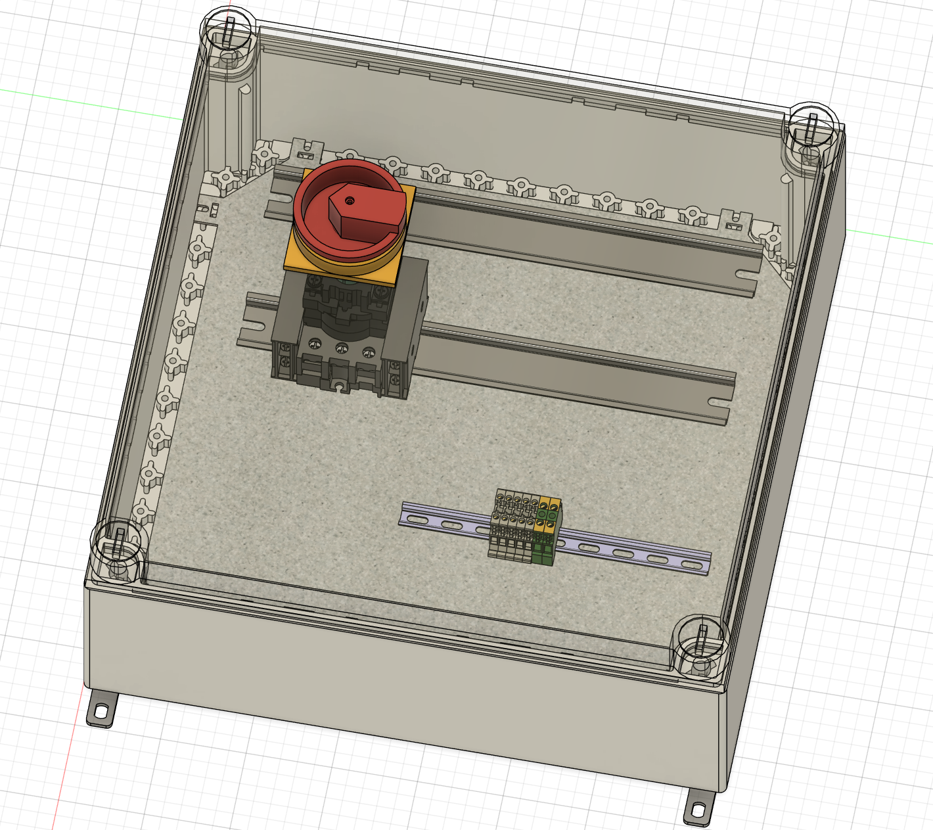
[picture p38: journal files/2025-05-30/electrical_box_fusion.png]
  
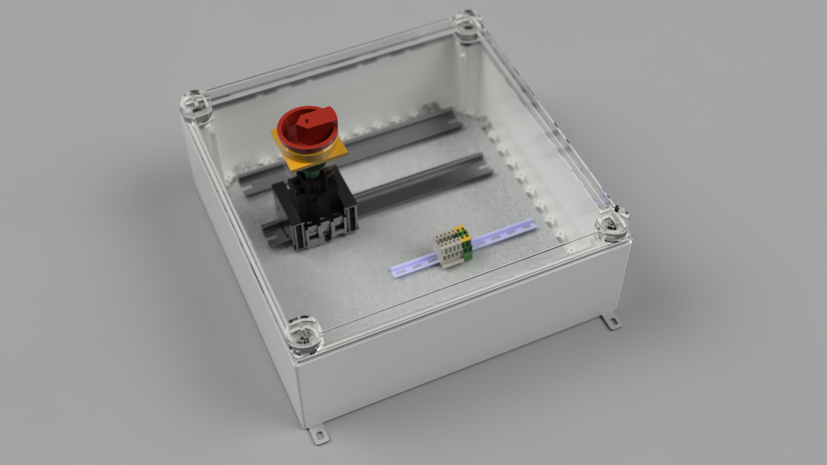
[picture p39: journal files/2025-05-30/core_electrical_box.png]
  
</p>

### Session 3 (2h 30m)

For the first sensor modul to design I decieded on the window contacts which are based on reed switches and magnets. These sensors will be designed for our greenhouse and the aluminium extrusions it uses. To attatch my 3D printed parts to the aluminium extrusions I thought of M3 screws and corresponding nuts. The case fo the reed sensor and magnet are designed in such a way that ti is possible to assemble the housing without screws just with the clips on the sides. 

<p float="left">
  
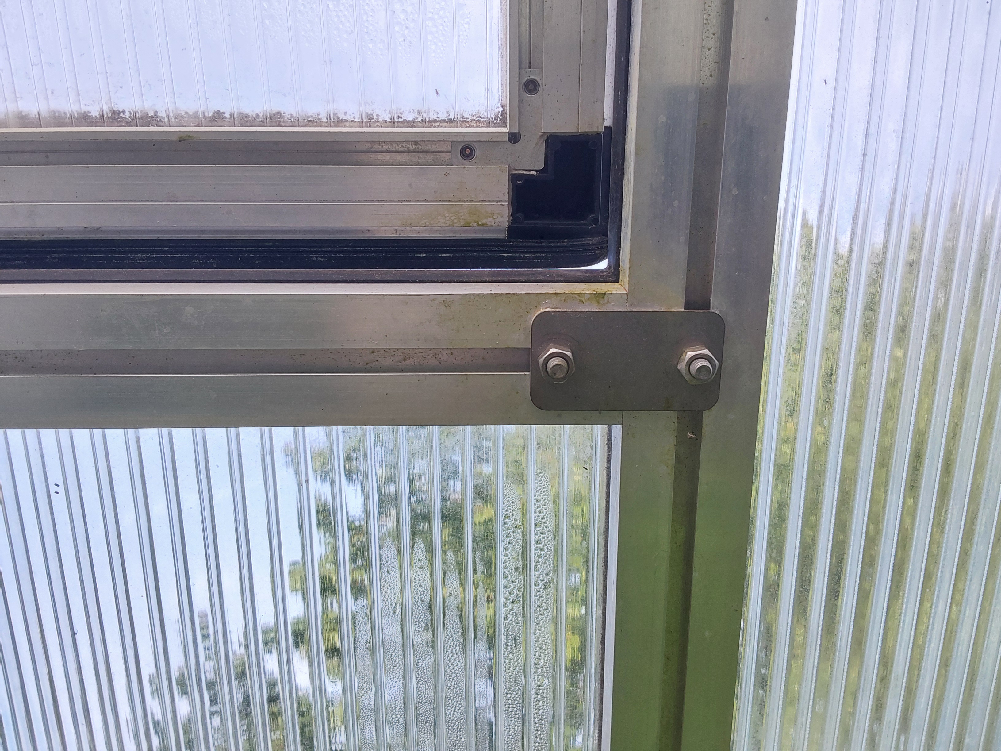
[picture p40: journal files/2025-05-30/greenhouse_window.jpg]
  
</p>

### Session 4 (1h)

I am going to desing cases for all components so they can be mounted on the existing DIN rails. But to build a case around my parts I first need them to be in CAD. Because my relais module is out of production and the screwholes are custom for almost every board out there I quicly sketched up mine. Besides I modeled the bottom terminal row completly like it is right now in real life. Additionally I added a 5V and 9V rail mounted powersupply. The 5V one is for the ESP and relais board while the 9V one is for supplying the solanoids with power. The solanoids will be controlled by the relais board.

<p float="left">
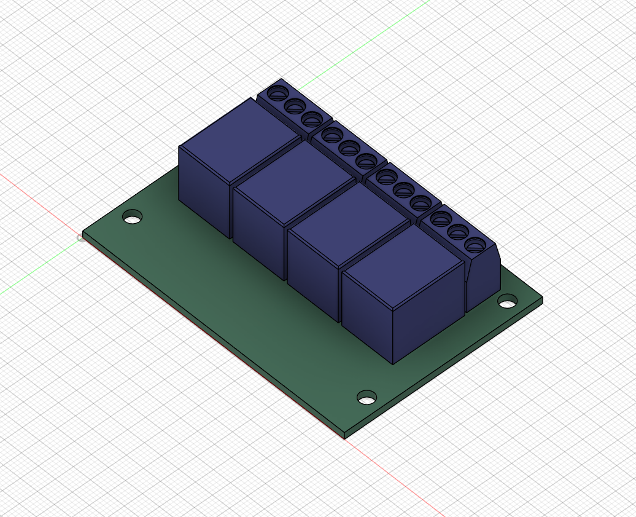
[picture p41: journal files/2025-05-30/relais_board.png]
  
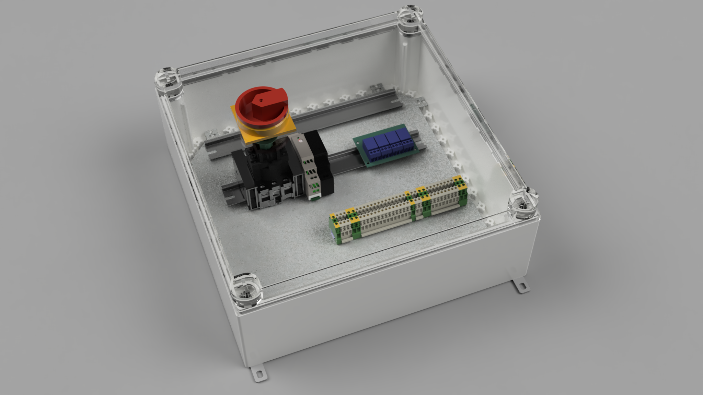
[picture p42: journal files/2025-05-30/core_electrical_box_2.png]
  
</p>

## June 5th (2h): add some branding and Dallas sensor module

### Session 1 (1h 30m) during live call

I thought my project could need some proper branding and logo to let the README look nice. As my go to software for vectorgraphics I used Inkscape to do the logo. As my Project is compatible with Home Assistant I started with importing the Homeassistant logo. For my logo I wanted something that is simple and matches the astetic of Home Assistant.

<p float="left">
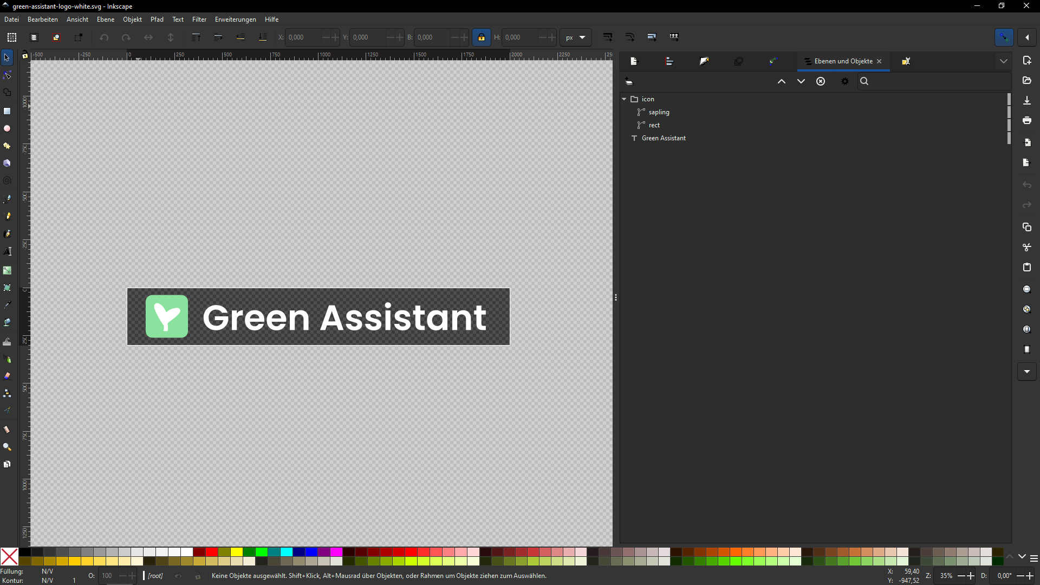
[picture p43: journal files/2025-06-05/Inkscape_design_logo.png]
   &nbsp; &nbsp;&nbsp;&nbsp;
  
  
</p>

### Session 2 (30m) during live call

I have added the Dallas temperature sensor module. Mostly it was code because the ground temperature sensors are already encapsulated. In my project two of those sensors will be used just for fun and because I have them laying arround. It defenitely will be interesting to see how the ground temperature is changing over the day.

## June 23rd (6h): desinging sensor modules

### Session 1 (2h)

After creating a cool loking logo and branding I decided to go on with designening the sensor and action modules. The next one in line was the light sensor module. Measuring light intensity might be really interesting to see in a greenhouse environment.



I also decided on using a new standardised format for each sensor and action module. Each of them has it's own Readme with a seperate BOM this should improve the experience for users who want to build a simialr project but don't need as many sensors.

### Session 2 (1h)

I have updated some sensor moduel READMEs now to accomidate the new format. Additionally I finished the homeassistant configuration for the window and door contacts. Some inforamtions form the window contacts module regarding 3D printing instructions was also copied.

Up until now I think the README for the window contacts is my favourit with its animated gif ot the CAD model and the BOM with parts at the top.

### small break

visiting the greenhouse and touching some grass outside :) aka not beeing glued to my monitor

### Session 3 (1h)

New sensor module! I have most of the parst already at home so Hackclub doesn't need to pay for them. One sensor that will be particularly interesting for greenhouse monitoring is a CO2 sensor which I unfortunately don't have. So now it's the time to add it to the project. It is is bit more expensive thatn a DHT22 or other sensor but with about 20$ also won't break the bank. Designing a mounting system was a bit difficult because I had nothign to measure of but I eventually found a datasheet with dimensions on it. In the end I decided to design a simple clamp over the sensor that can be mounted to the aluminium extrusions with two M3 screws and fitting nuts.



### Session 4 (1h)

One of the last sensor modules. Yeah! I have soldered some wires on the DHT22 sensor I had in my drawer. Forunately The sensor as a 3mm hole at the top so a M3 screw fits perfectly and I don't need to desing a custom mounting solution. I thought about adding a 3D printed shield for the sensor to protect it against direct sunlight. Currentyl it will be mounted behind the aluminium extrusion of the greenhouse so direct sunlight hopefully won't be an issue.

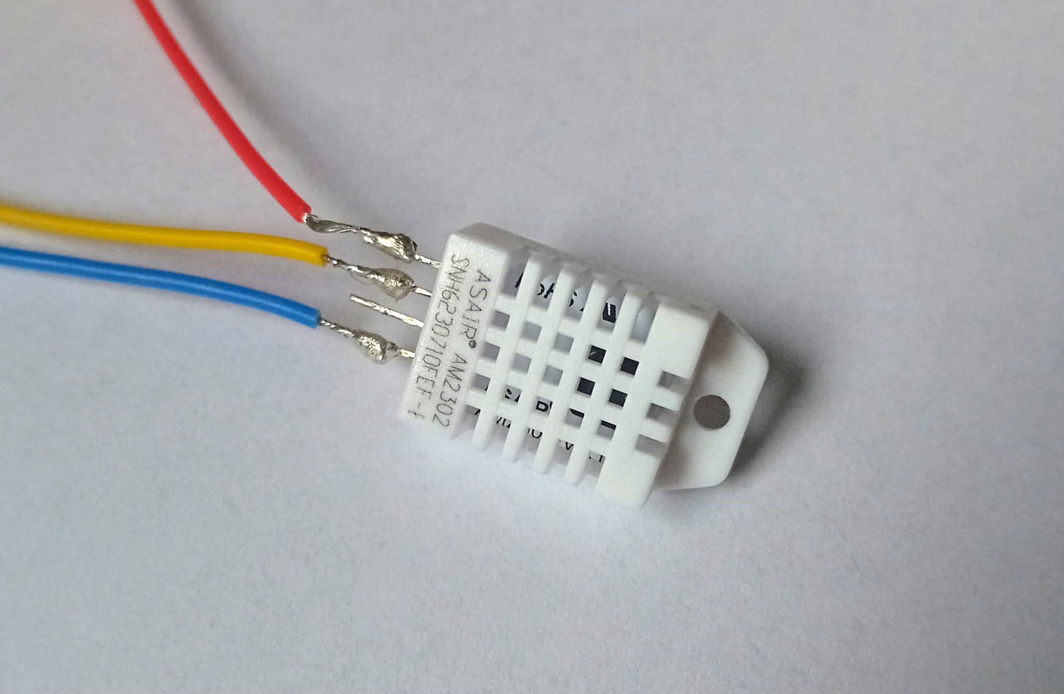
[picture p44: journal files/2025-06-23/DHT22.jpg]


### Session 5 (1h)

For now the last sensor module is complete. Prpbably the most important one for a greenhouse automation, the soil moisture sensors. i decided to go with capaciative ones pecause they dont degrade or not as easealy as some others with metal rods. Additionally I had themy lying around so why not use them :). The Homeassistant configuration I build also contains the calibration logic that has to be used once to tell the sensor what is dry and what is wet. Somebody rebuilding my procet can therefore easily build a similar setup.

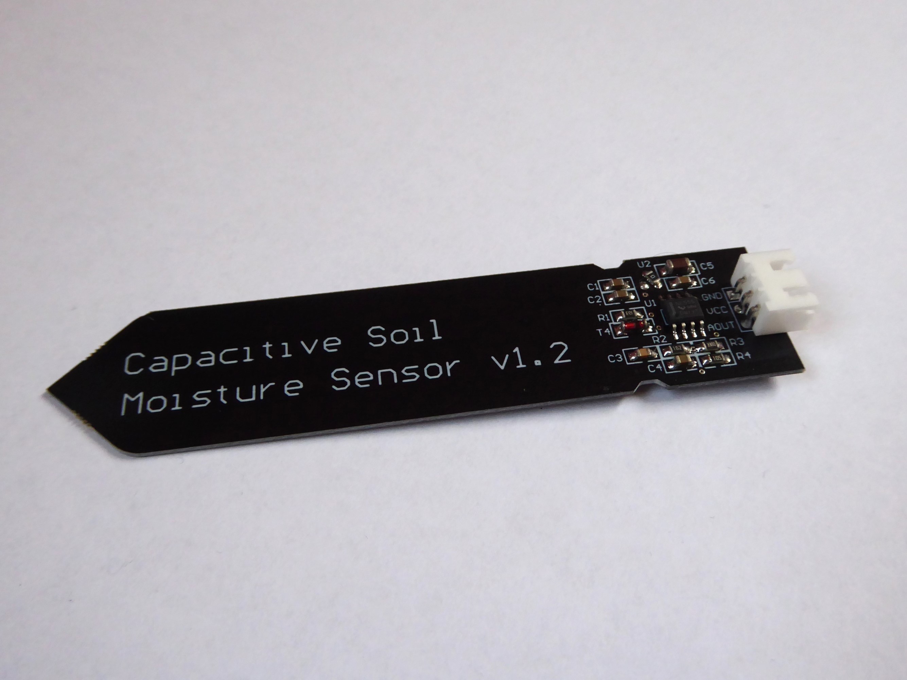
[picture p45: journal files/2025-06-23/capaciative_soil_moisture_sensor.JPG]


## June 24th (13h): Setting up Homeassistant

### Session 1 (3h)

I grabed my Raspberry Pi 4 B and an SD card and got right to installing Homeassistant for testing. In the future I will be running Homeassistant inside a VM on my NAS which is running TrueNAS Scale. While the image was downloading and later on installing on the Pi 4 I put togetehr a first prototybe with all the sensors I already have. I am going to use an ESP32 with ESPHome on it.

I directly connected the RPi4 to our Router via internet and noticed that it is actually supported by Homeassistant automaticaly and I can now monitor aour nethwork useage via Homeassistant, cool stuff :). Under Add-ons I have now installed the ESPHome Device Builder. Now I can begin building a full yaml config with all the snippets I already have inside the individual sensor module folders.  

<p float="left">
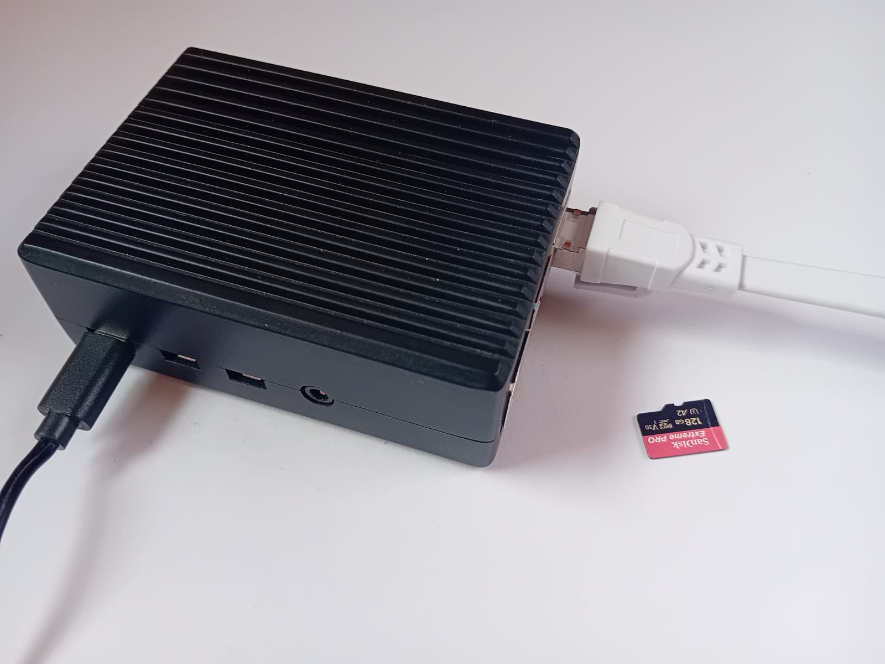
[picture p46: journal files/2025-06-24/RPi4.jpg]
  
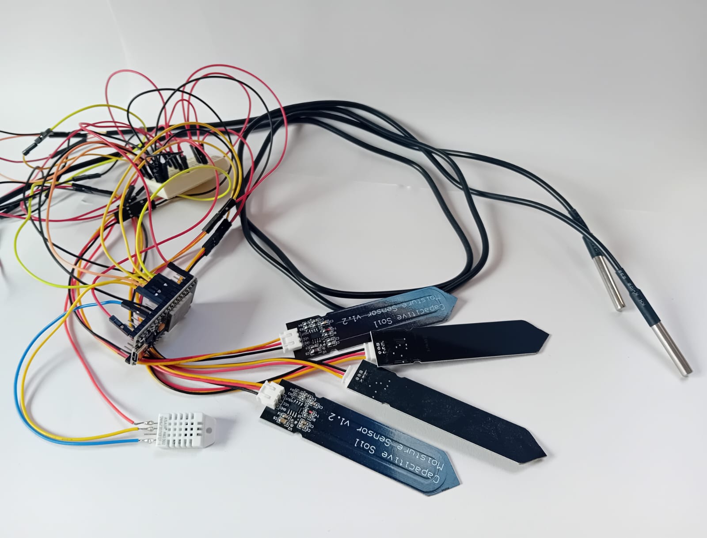
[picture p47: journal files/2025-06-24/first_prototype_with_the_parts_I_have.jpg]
  
</p>

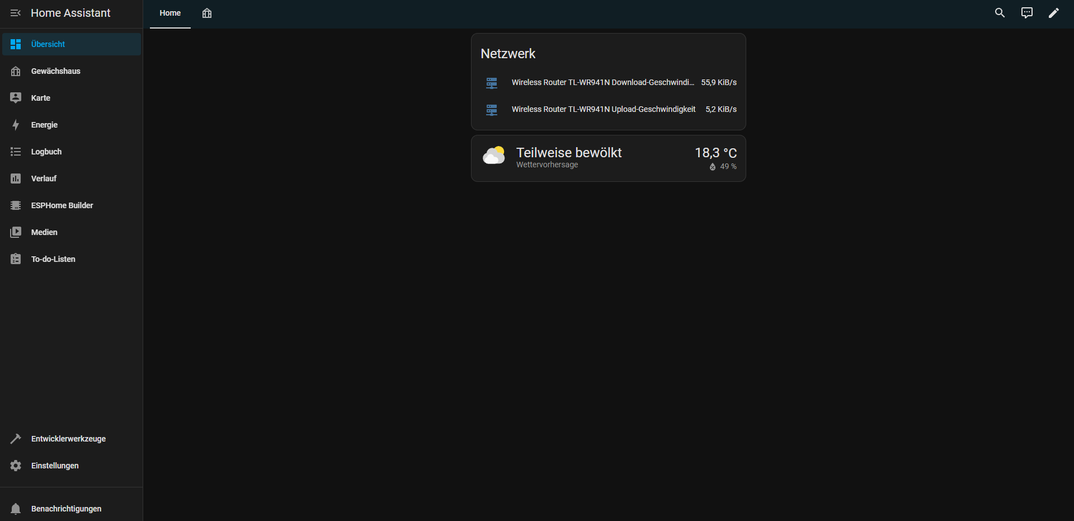
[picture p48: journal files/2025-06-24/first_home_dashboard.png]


### Session 2 (5h)

ESPHome is now setup and running with the sensors I currently have. To get it working I put together all the small snippets I already had written for each sensor module. The current setup consists of 4 soil moisture sensors, one DHT22, two DS18B20 soil temperature sensors and a realy board.

<p float="left">
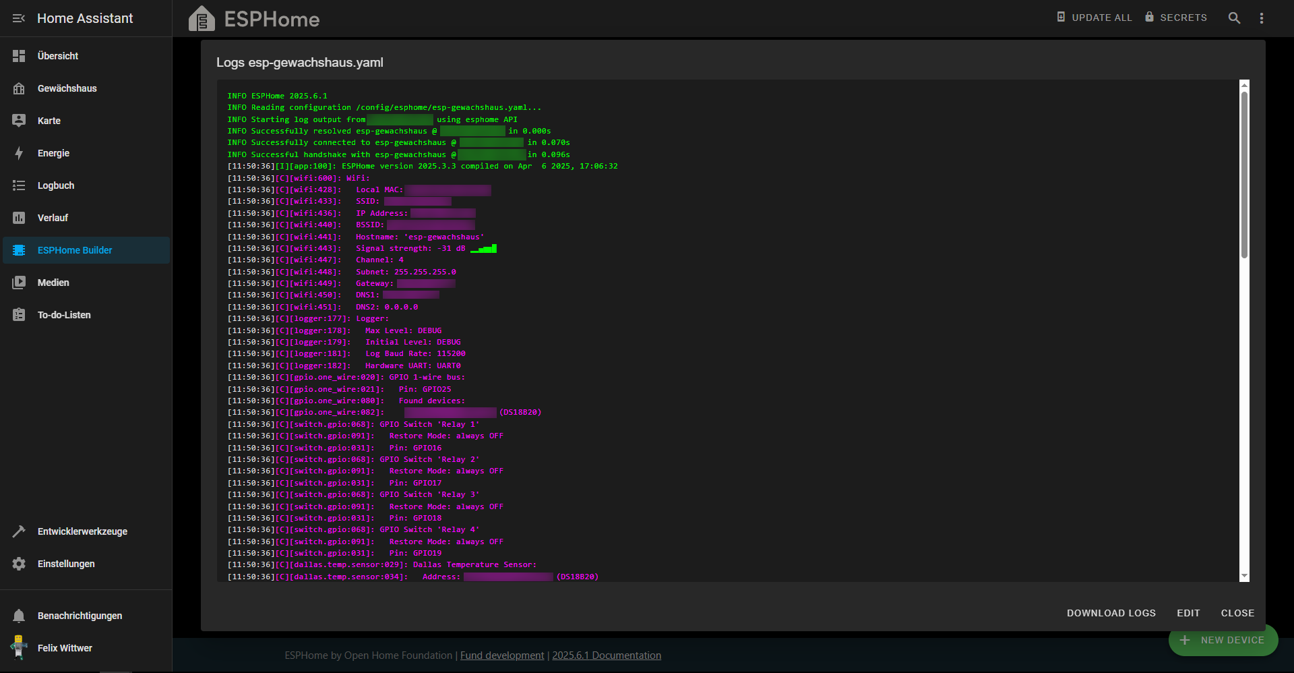
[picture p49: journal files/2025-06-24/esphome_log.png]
  
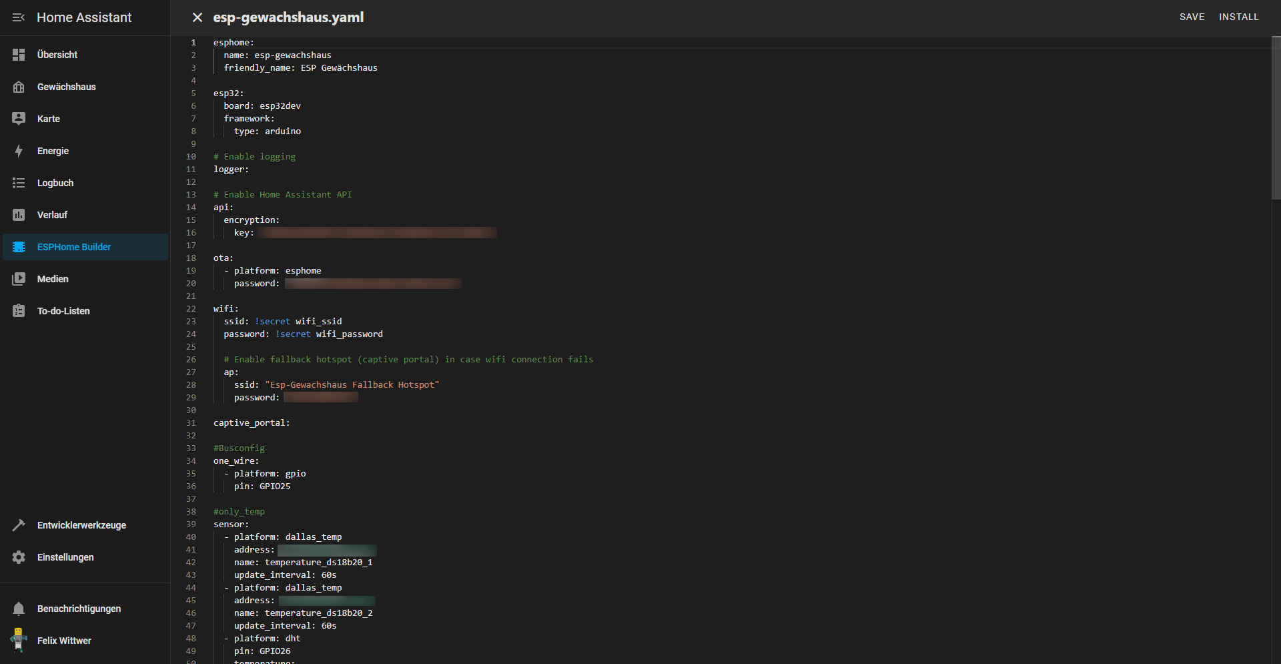
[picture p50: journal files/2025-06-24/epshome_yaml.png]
  
</p>

After a lot of tinkering I got a cool dasboard together and it is working! especially styling and placing the sensor values on the map was difficult. It now correctly displays the values of the sensors I have currently set up. Because I have multiple zones for the irrigration and sensors I decided to use Homeassistants stack and map components. A notmal stack of components wouldn't be so resonsive (I want to us it on mobile and desktop and later on maybe on a dashboard) I decided to split things up in collumns and addes some stacks in beetreen that can be easialy resized by the device on the corresponding platform. I kind of fell in love with the dashboard maps and created a floor plan of our greenhouse to get a better Idea where the sensors are located in real life. There is now a map for genreal environment sensors, soil moisture sensors, irrigation system and ground temperature sensors. As a small additon I added small badges at the top of the page to have the irrigation system easialy accesible.



### Session 3 (4h): main PCB design

Since my prototype cabeling is an absolute mess and everything should be organized inside the electrical box I designed a shield pcb for the ESP32 S3 I am using. I acutally only need the PCB without assembly because I have most of the parts and from my experience JLC PCB most times does not have screw in terminals with a 5mm pin distance. Furthermore assemby is unresonably expensive for some parts that aren't smd. I intentionally designed the resistors to be non smd so they can be switched if needed. I don't know maybe the very humid enviroment isn't the best even if mostly sealed inside a the electrical box. Additionally I don't know weatcher I need the other pins of the ESP32 in the future so I decided on giving them some headers.



<br>

<p float="left">
  
  
</p>

### Session 4 (1h): PCB mount deisgn

Becaus the PCB will defenitely wont float and will need some mounting hardware I did just that. If you are wondering how I pulled taht of especially with the random hole design of my PCB (I havent bothered to make something with nice measurements and just placed them here no traces were), I exported the PCB in KiCad to a wrl file and opened that with Blender inside Blender I exported it to an stl file (makre sure to chosse scale 1000 or else your pcb will just be a fractions of milimeters long) and importet this into Fusion 360 where I traced the holes from the stl model.



## June 25th (4h): adding irrigation system and finishing of

### Session 1 (1h): mounting for relais board

My costom PCB already had a mount but to make it perfect also the relay board needed some mounting hardware. In the end I decided to attatch the PCB via 15mm long M3 screws and correspondign nuts.



### Session 2 (1h): planning for irrigation tubing

Since all electronic parts are done now we have to think of a way to water your beloved plants inside the greenhouse. I decided to go with a 4 in 1 solanid that is perfect for my 4 zone watering system. Between all the components 10 mm PVC tubing will be used. All the individual parts for connecting the individual tube pieces will be 3D printed. So for each plant you need a t piece and a nozzle to water it. I will maybee adjust the nozzle size in the future but for now it should work. Anothe Idea might be to make kind of an l piece at the end to save on the end piece but then the entife l piece nedds to be redesigned and not just the nozzle.

<p float="left">
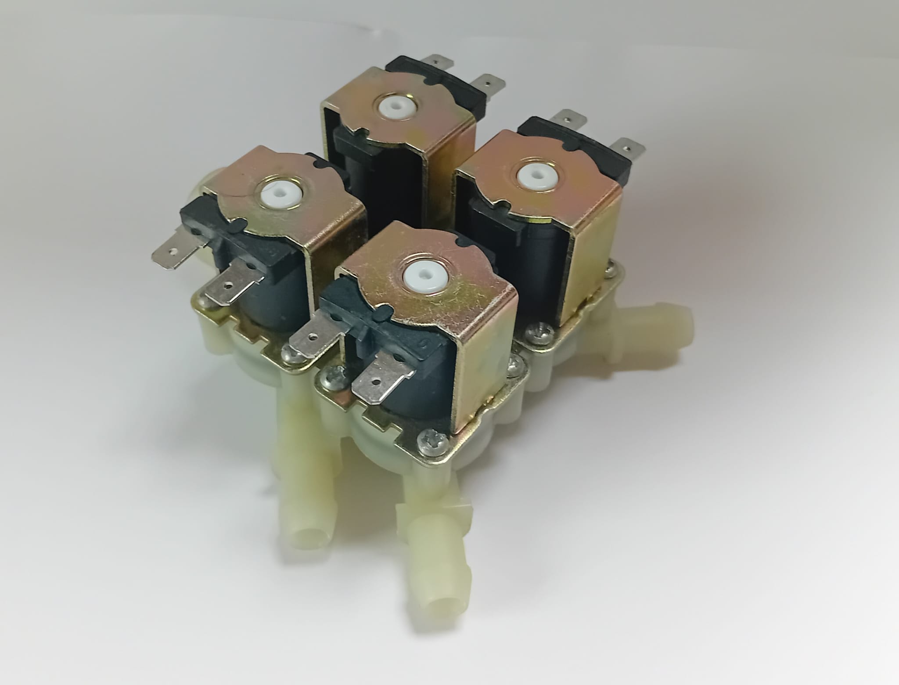
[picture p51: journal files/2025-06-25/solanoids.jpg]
  
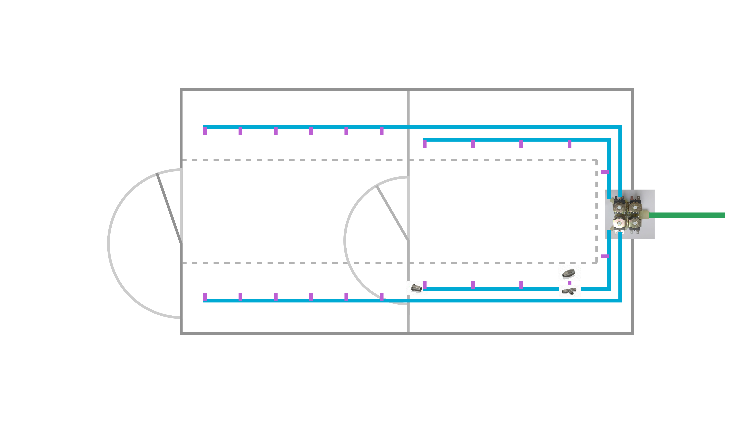
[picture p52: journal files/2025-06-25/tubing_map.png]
  
</p>

<p float="left">
  
  
  
</p>

### Session 3 (2h): adding a wiring diagramm

Most wiring is done with the PCB but all the sensor still need to be connected. Here comes the electrical box into play. I am going to use the old already in place DIN rails to mount everything from the relais to the custom PCB inisde. All the sensors will be outside of the box in the places where they need to be. Besides the wiring diagram I finisted the design of the electrical box and arranged its components.




### Session 4 (1h): writing some documentation and making it easier to create your custom Green Assistant

Because it could be difficult to understand the projects structure I designed a small diagram on where to start and how to configure your Green Assistant. With this map someone else could easealy start building theor own smart greenhouse. Besides that I extended the main README file a bit.



## June 30th (2h)

### Session 1 (2h): researching parts and creating BOM

As one of the last steps of the planing phase I finished the BOM list of the project luckily I have most parts of my BOM already at home and also can 3D print parts at home. Fort somebody that is going to build his own system it is imortant to nate that you defenitely don't need a industrial grade waterproof electrical box but we already had one so why don't use it. But for anyone else: you will be fine with buying a DIN Rail and mounting your stuff to it.

### Session 2 (2h): doing some final touchups and completing ESPHome config

I have noticed that I have forgotten to add some codesnippets form the individual sensors to the main ESPHome config so I did that now. I have designed and coded all parts for the window and door sensors but forgot them on the PCB. This isn't bad at all because I thought about having all remaining pins pined out so I can add some stuff later on. The PCB has the perfect formfactor and I will not change it now because of space inside the electrical box. The sensors can still be added easily.

## July 17th (2h) designing, printing and installing cable clips

To cleanly mount the ethernetwire I choose to the greenhous aluminium extrusions I designed some cable clips that simply could be twisted into the slot. After designing and testing I made a second improved final version. The clips then were printed on my SLA resin printer.

<p float="left">
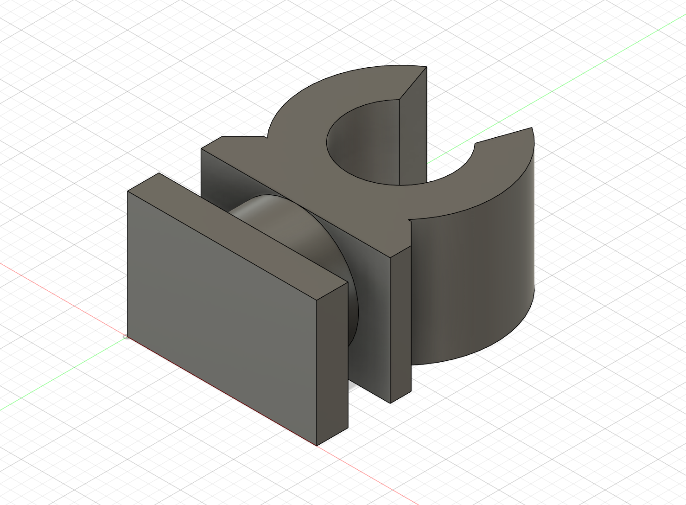
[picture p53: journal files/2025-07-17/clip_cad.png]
  
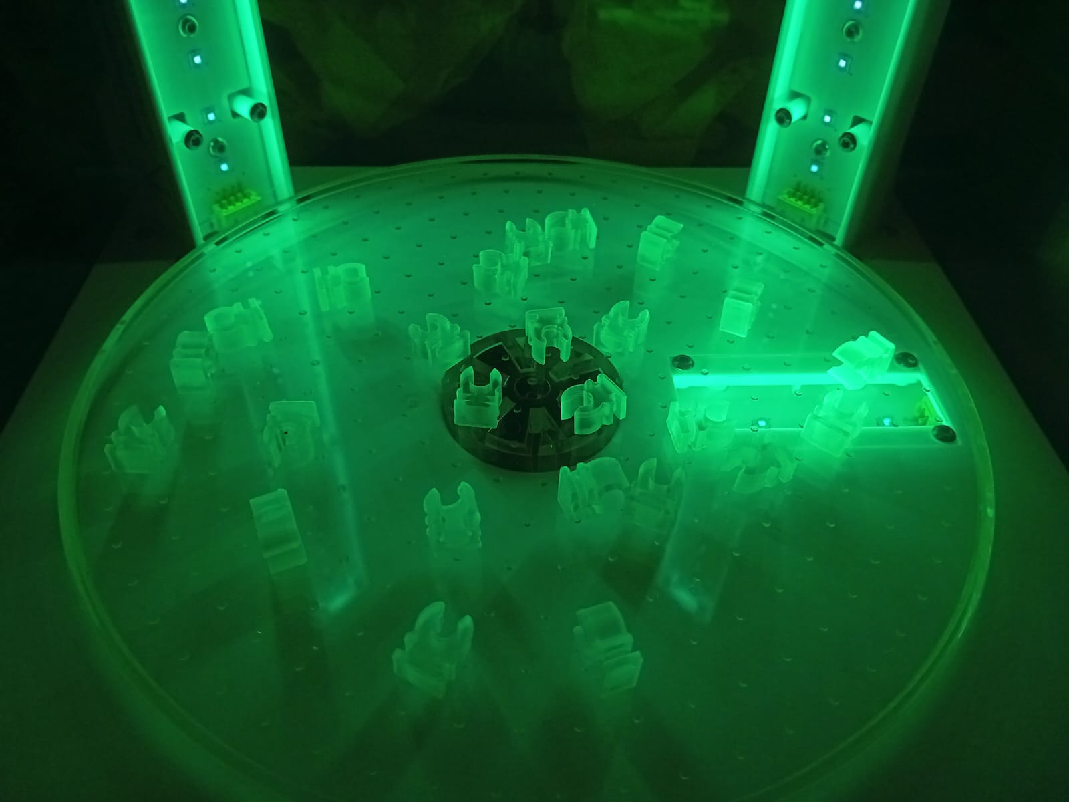
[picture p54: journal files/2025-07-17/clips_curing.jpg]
  
</p>

## July 18th (1h 30m)

### Session 1 (1h) PCBs and parts finally arrived

The PCB and other parts finally arrived today. As a first step I populated the PCB with all the parts. From today on my 3D printer will run constantly to print all the parts.

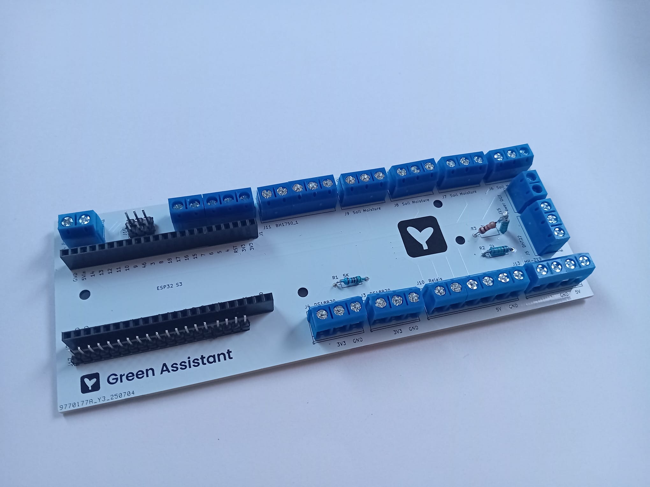
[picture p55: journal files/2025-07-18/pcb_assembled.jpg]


### Session 2 (30m) M3 nut adapter

After noticing that the slots inside the aliminium extrusions of my greenhouse are a bit to large to fit M3 nuts I designed an adapter to widen its footprint and stil use the with all the current sensor module designs. This save some time because I don't need to modify all sensor moduels and don't need to buy new screws.

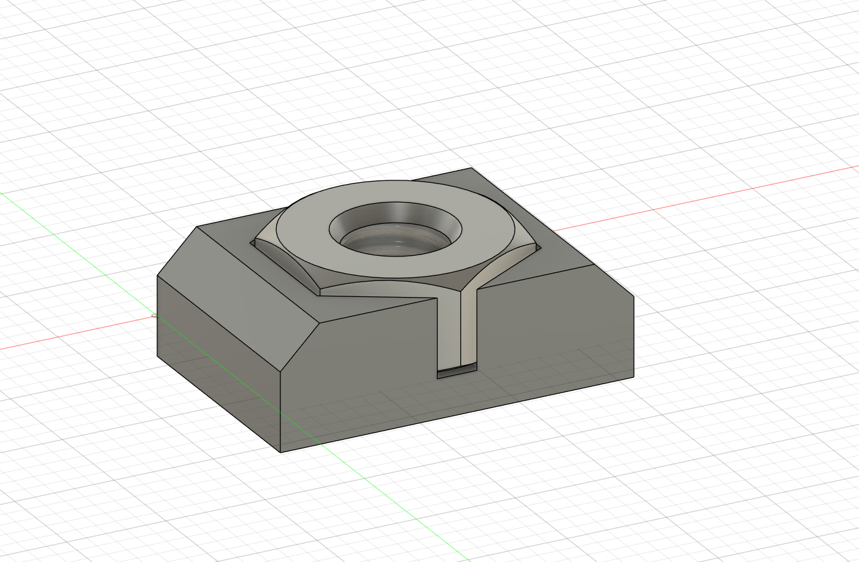
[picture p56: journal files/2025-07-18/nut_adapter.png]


## July 19th (2h) testing the PCB

I just finished printing the mount for the CO2 sensor. While the printer was doing its stuff I put all the wires in place to test if all the sensors work. Yeah say so they work now but it took a while to get them work. First of all the PCB needed to be powerd via the 5V terminal which is the case in the final version but not now. took me a while to figure this out but sensors don't work without power :). Secondly the RX and TX pins of the CO2 sensor were labled wrong in the datasheet. And It took me a while to figure that out.

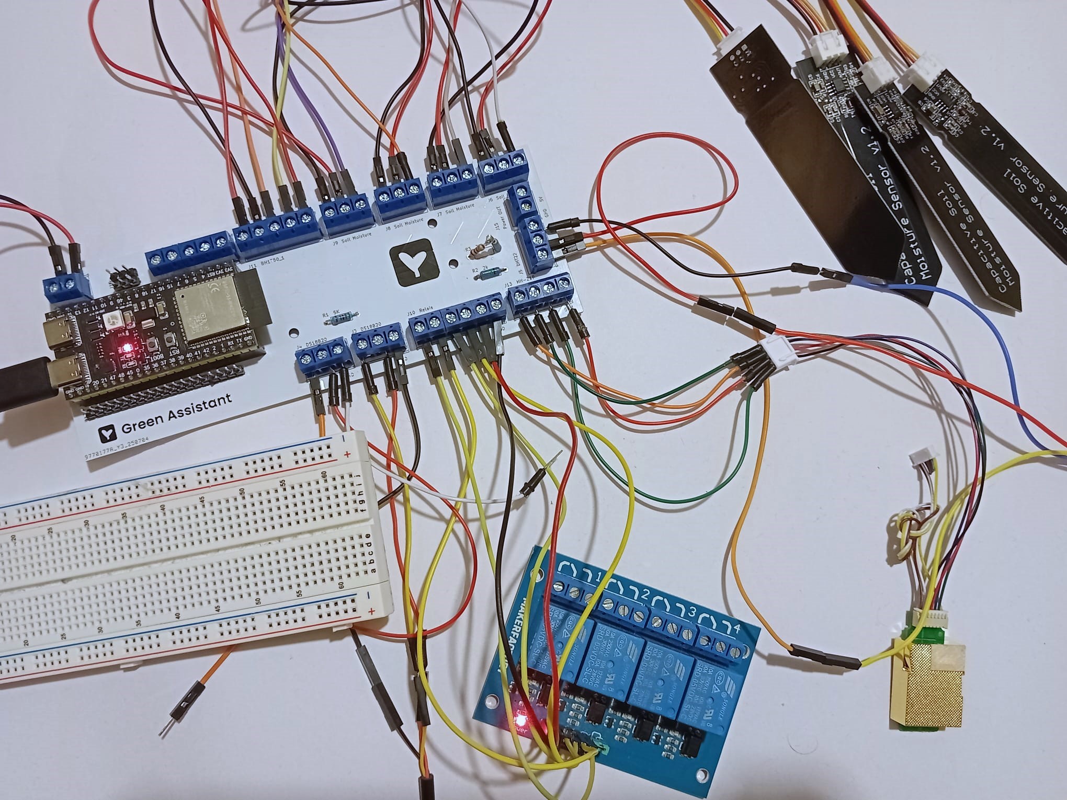
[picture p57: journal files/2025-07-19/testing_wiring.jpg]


## July 21st (4h) start wiring the electrical box

I would have never thought that wiring inside the electrical box takes soooo much time. It tooke me 4 hours now to wire up a good portion of the sensors. The rest of the sensors will be done tomorrow. Besides wiring I also picked up some additional tubing stuff for the irragation system.

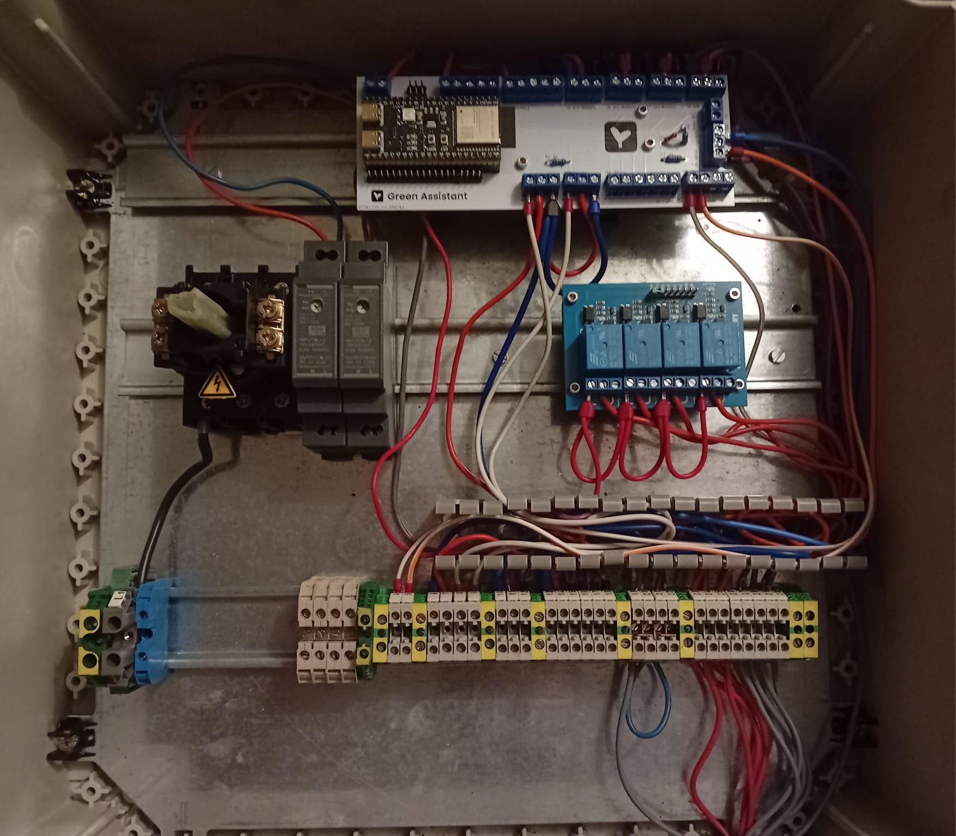
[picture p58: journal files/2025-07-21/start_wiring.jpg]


## July 22nd (6h)

### Session 1 (3h) finishing sensor wiring

Today I finally finished wiring all the individual connections from my cusom PCB to the screw terminals whicht are clipped to the most bottom DIN rail. The last step in finishing the electrical box will be to hock it up to mains power and install a standard receptacle plug. After that the sensors only need to be connected via a shielded ethernet cable to the bottom terminals.

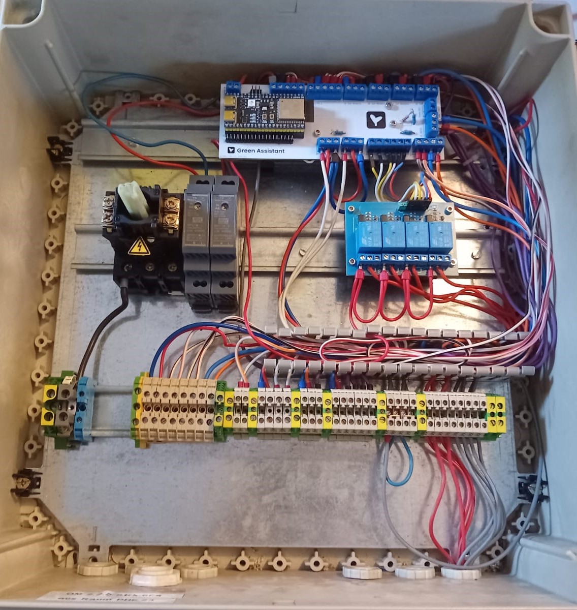
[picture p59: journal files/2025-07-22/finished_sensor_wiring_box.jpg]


### Session 2 (3h) start making quick/emergency guide

I now also started to write or actually draw a small manual for the electrical box. So if someone else is going to modify, maintain or expand the system he doesn't get electrecuted immediately. Besides that there will also be a sheet wir instructions on how to turn zhe system on and what the error codes mean. These three to four sheets will be laminated and kept near the box outside.

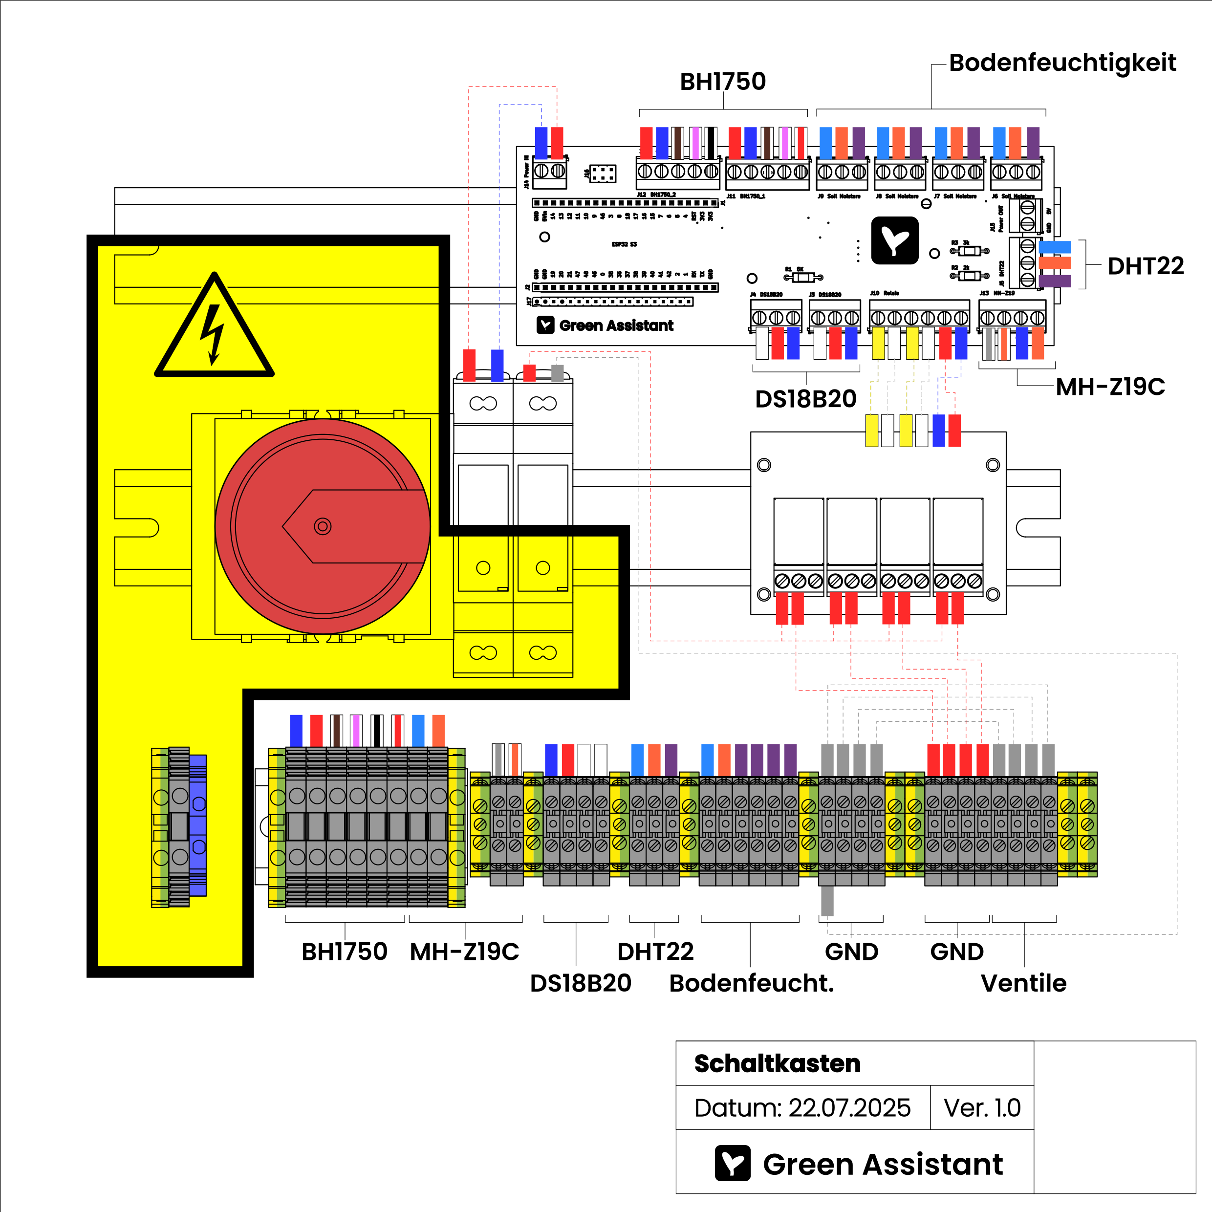
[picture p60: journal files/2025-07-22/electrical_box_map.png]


## July 23rd (3h) finishing wiring to mains power and install electrical box inside the greenhouse

Finished the last fer wires for connection to mains power and installed the electrical box inside the greenhouse today. Took a bit of time digging two holes for the steel L extrusions. Dirlling the holes tof mounting teh box took sume time due to blunt drill bits :) but eventually found a sharp one which made this step much easier.

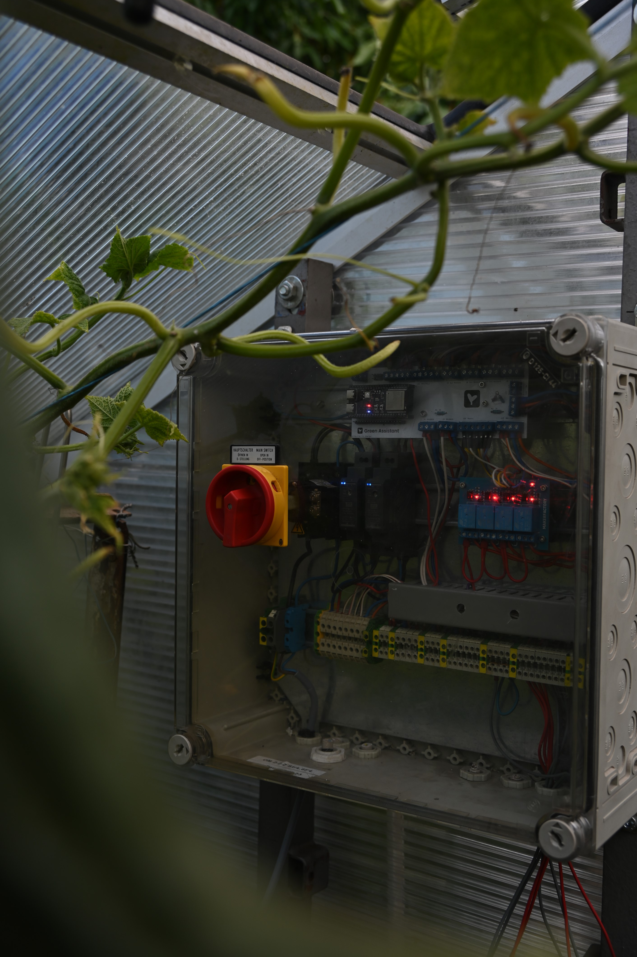
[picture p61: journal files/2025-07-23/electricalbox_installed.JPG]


## July 24th (8h)

### Session 1 (2h) Pluming

So yesterday I finished installing the electrical box. Today I started with laying out a new garden hose from our pump to the greenhouse. To integrate it into our existing garden hose system I needed to build a second howse branch from the existing system which can be shut of with a ball valve.

<p float="left">
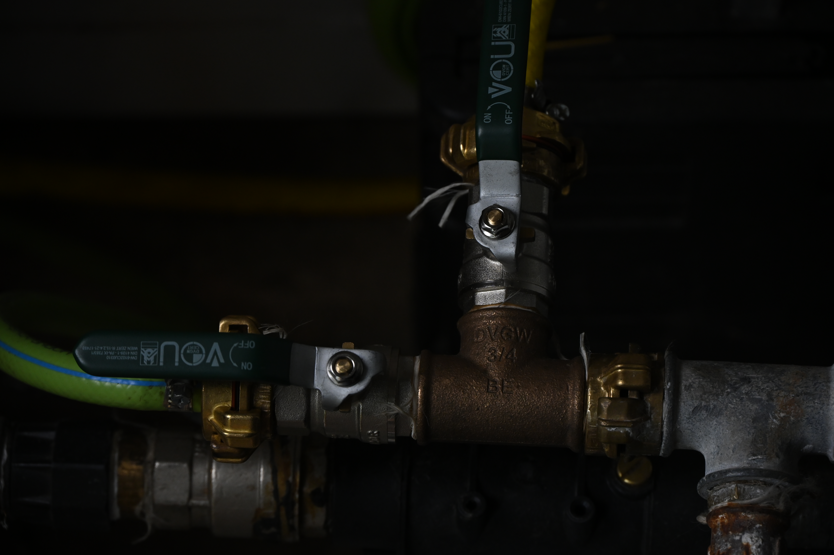
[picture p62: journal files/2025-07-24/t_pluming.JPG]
  
  
</p>

### Session 2 (2h) installing the irrigation system

To water all the plants inside thee greenhause I used some simple PCV plastick tubing. Originally I wanted to print T pieces and nozzels for this tubing but went for just tieing it straight to a bar and making some holes with a screwdriver in it. It is defenitely a much easier solution and the tubing is free of additional plastics so it sould be drinking water quality save.

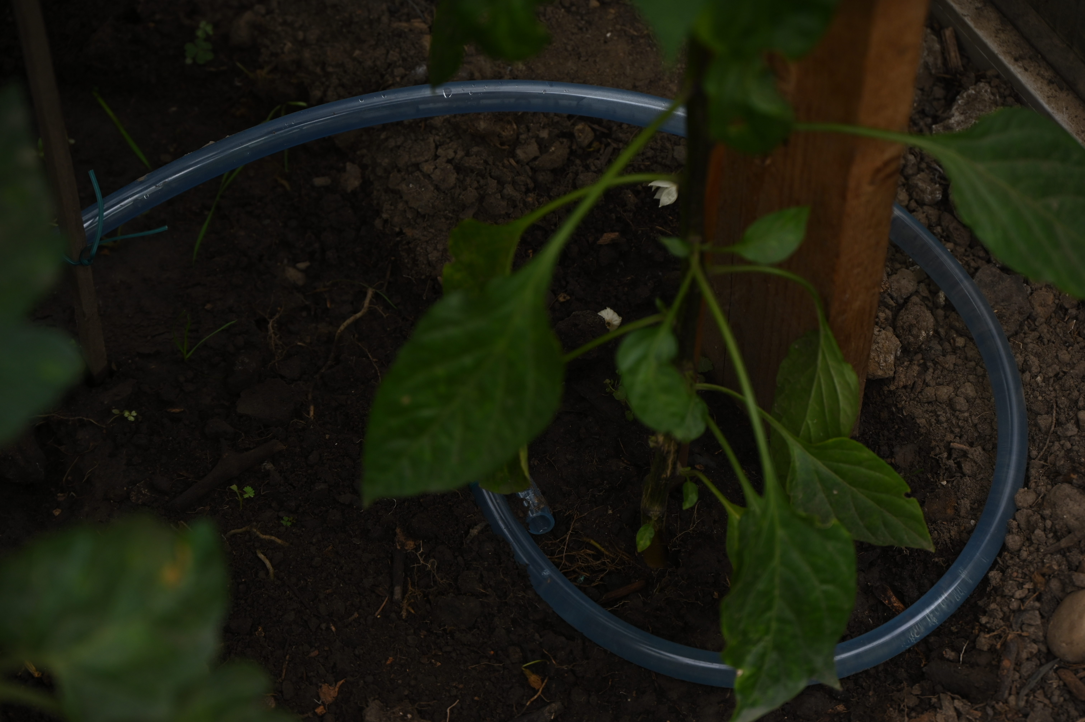
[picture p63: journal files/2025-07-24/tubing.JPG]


### Session 2 (4h) Wiring a few sensors

For my last task for today I choose to wire up some sensors. After making a mistake in the wiring and redoing alsmost verything I managed to get both ground temperature sensors working. Three soil moisture sensors are already connected but dont seem to work properly. But wiring up the remaining sensors and making the sensors work is a task for tomorrow. Maybe a simple calibration could solve the issue.

<p float="left">
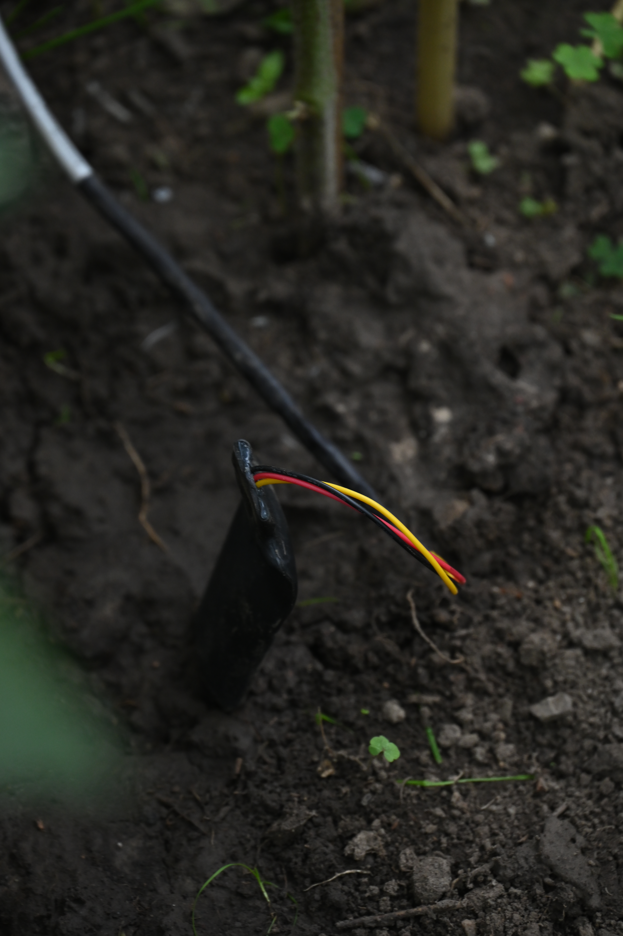
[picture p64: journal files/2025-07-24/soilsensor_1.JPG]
  
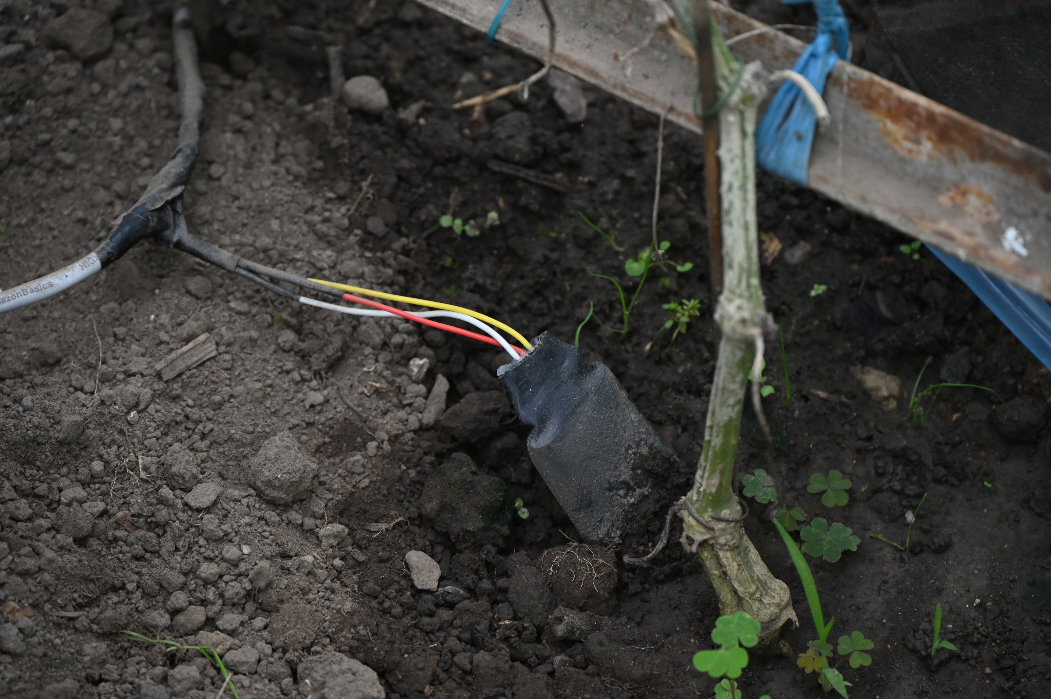
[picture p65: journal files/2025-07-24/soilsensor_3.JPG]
  
  
</p>

## July 25th (6h 30m)

Status update: Most :) of the installed parts already work perfectliy aka the irrigation system which today run two times perfectly. During some troubleshooting I also confimed that the large shrink tubing with some kind of hot glue in it is actually acually waterproof.

### Session 1 (3h) adding soil moisture sensor and CO2 sensor

I succesfully wirde up the last soild mosuture sensor for zone one. Additionally I precut all wires for the remaining sensors and fixed them into place by using my cool twist in clips for the aluminium extrusions. Surprisingly the CO2 seonsor worked from the beginning without any issues. Due to the housing for the light sensor not beeing printed yet I soldered a JST connector on the ent of the wire and sealed everything with some shrink tubing.



### Session 2 (3h 30min) troubleshooting

Two of the soil moisture sensors are not working so I cut the shinktubing open to se what is wrong to my surprise the wires seemed to be connected correctly even after coninuity testing it. As I later on found out, the sensors need to be a minimum amount of wet or deep inside the soil and mine werent. After remaking the connections and sealing the sensors with the big shrink tubing they worked. In addition to the harwdere fix I also updeted some parts of the software to accomidate the new voltage levels and correct caluclation of the percentages. In the end I got the soil sensors to work. The soiuld temperature sensors work mostly fine but simetimes the think the soil is at 85°C or has no temperature at all which is defenitely not the case. A reeboot of the ESP resolved the problems everytime.

## July 26th (4h) adding light sensor and doing some software stuff

### Session 1 (1h) add BH1750

Took me some time to get the sensor working. Turns out I probably wired up everything correctly the first time and was to imapcient to wait until ESPHome fulli registered the I2C connection to the sensor. After lots of trying I finally got it working and the sensor is now providing really nice and clean measurements.



(image before I wired everything up nicely :] in case someone asks)

### Session 2 (2h) doing some software configuration stuff

Since the irrigration system is in place now I added a routine for watering the greenhouse for now on a fixed schedule and later in response to the soil moisture data. For now there is a routine for the morning and evening. Both get activated everyday but can be manualld disabled for the day if chossen so. (In case it was raining all day and the soil is still wet)



### Session 3 (1h) configuring the EPS32s WS2812 LED

For fun and as a future status indicator I wanted to interface the builtin WS2812 on the ESP32 S3. After getting the GPIO Pin right it worked straight away. I can succesfully chnage the brightness and hue of the LED. And say so the LED is pretty bight in the night it can light up the entire greenhous section where the electrical box is located.



## August 5th (5h)

### Session 1 (3h) redesigning and printing window and door sensors

I have noticed that my system with the clips on the 3D prints didn't work that well so I designed a new version of the door and window contacts that uses screws (actually the same ones that are already in the BOM). After I finished designing them and needing to make a second iteration that finally worked I started soldering the cable tree for the sensors.

### Session 2 (2h) debuging and fixing the sensors

Both of the window sensors worked perfectly on the first install but the door sensor wasn't functioning properly. When first installing it sounded like I cracked the glass ampule of the reed switch slightly and as it turnes out this was the case but it took me a while to notice because you couldn't see the crack direcktly only the resistance values were of as I later discovered. Replaced the Reed and it works now.

<p float="left">
  
  
</p>

## August 6th (2h) filming the video and getting ready for final submission

After I finished the sensors yesterday I now only needed the video and a post for the final submission. Video was a bit difficult because I needed to hold my camera in one hand while controlling/ demoing the grennhouse with my smartphone on the other. In the end I managed to film everything and recorded a voiceover.

Reddit post can be found here: https://www.reddit.com/r/Esphome/comments/1mje8r1/yet_another_automatic_greenhouse_but_a_bit/

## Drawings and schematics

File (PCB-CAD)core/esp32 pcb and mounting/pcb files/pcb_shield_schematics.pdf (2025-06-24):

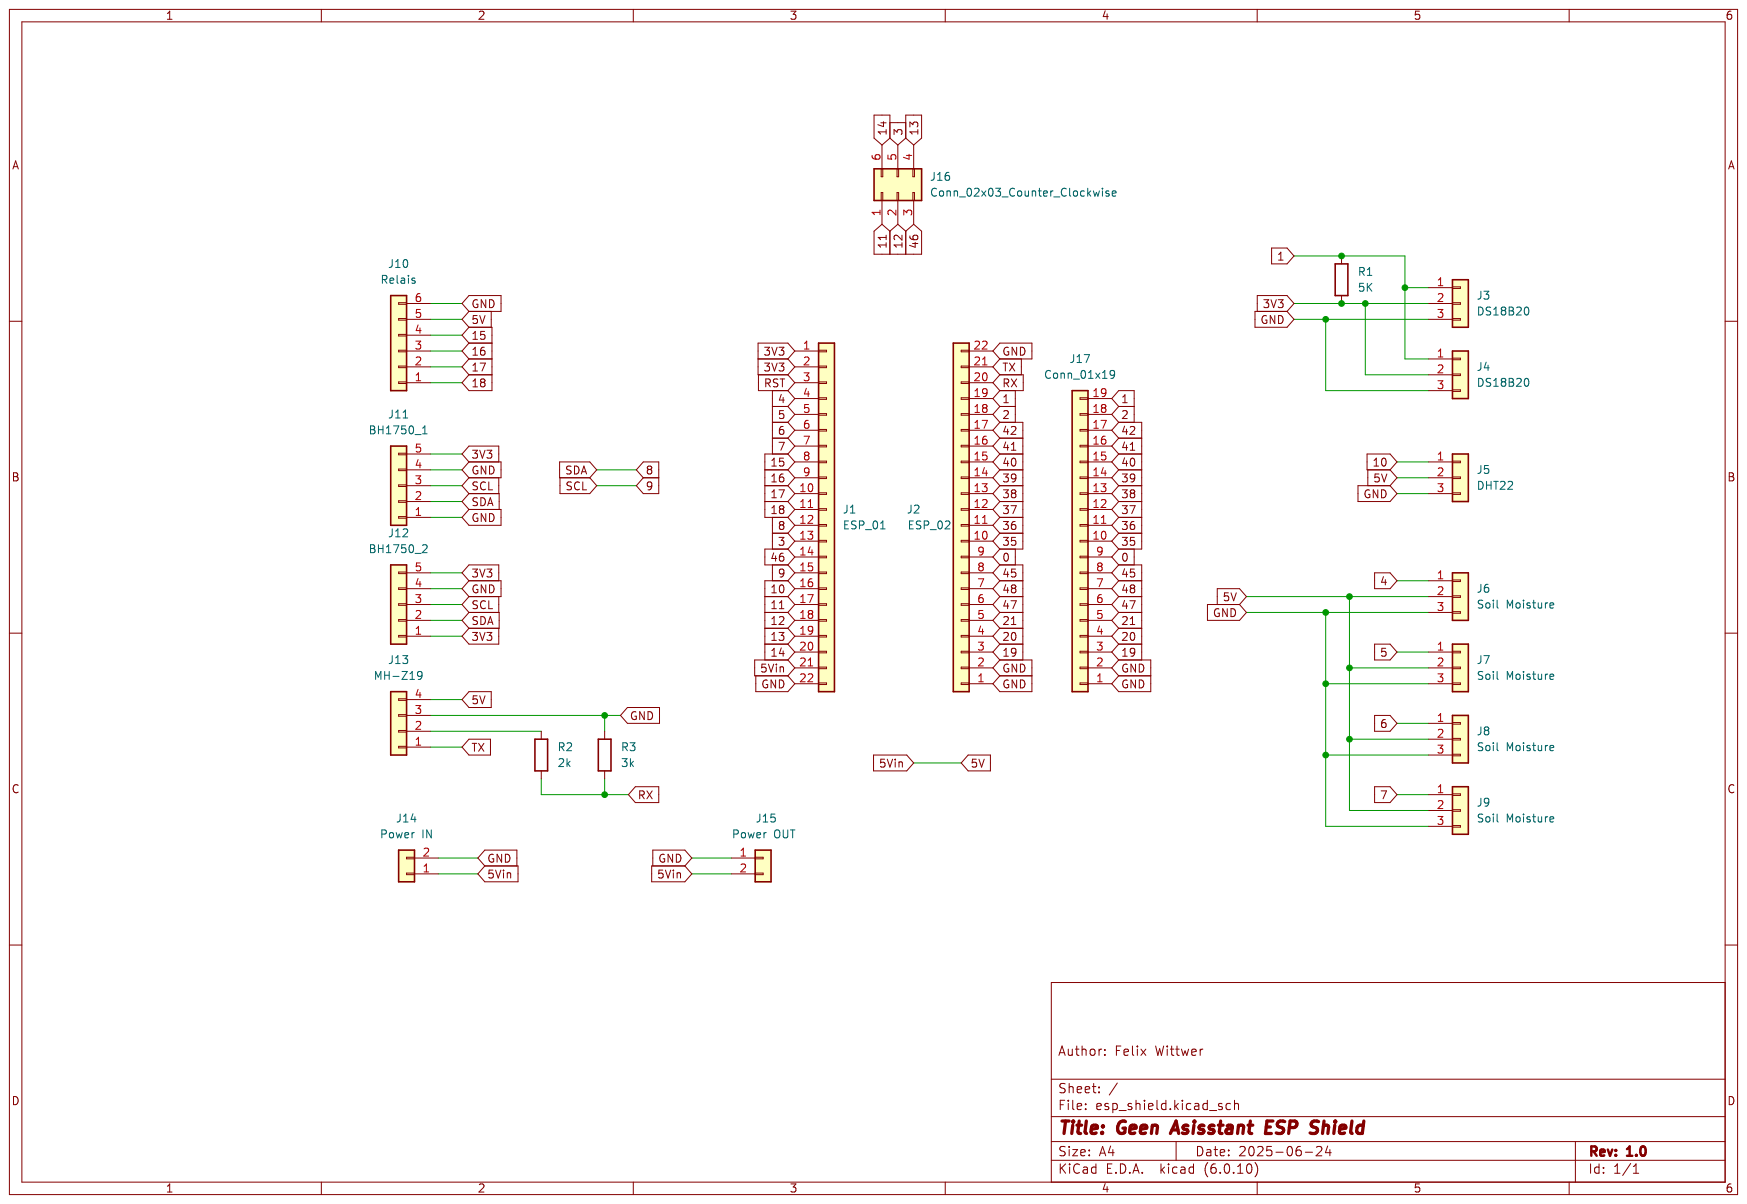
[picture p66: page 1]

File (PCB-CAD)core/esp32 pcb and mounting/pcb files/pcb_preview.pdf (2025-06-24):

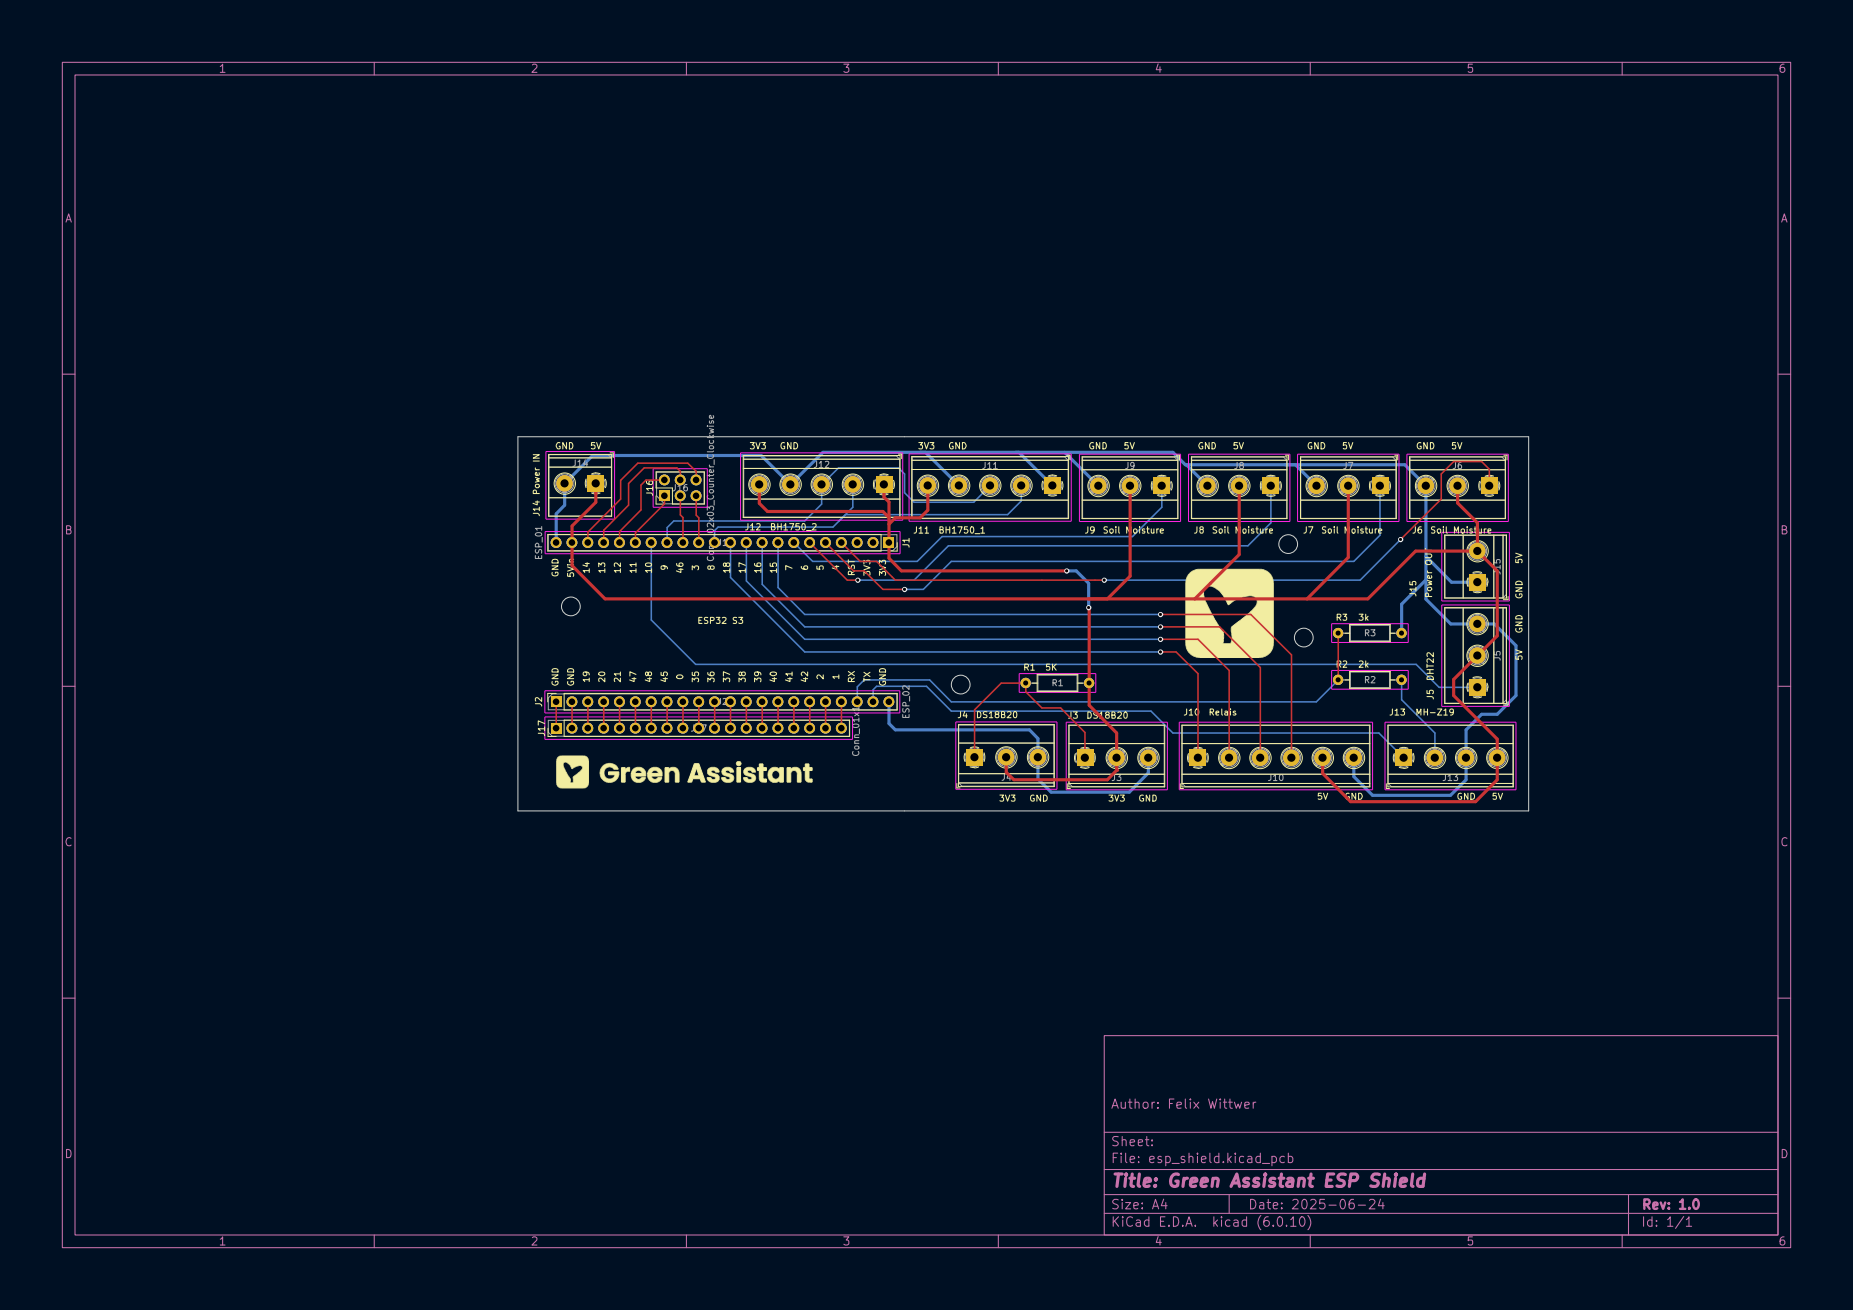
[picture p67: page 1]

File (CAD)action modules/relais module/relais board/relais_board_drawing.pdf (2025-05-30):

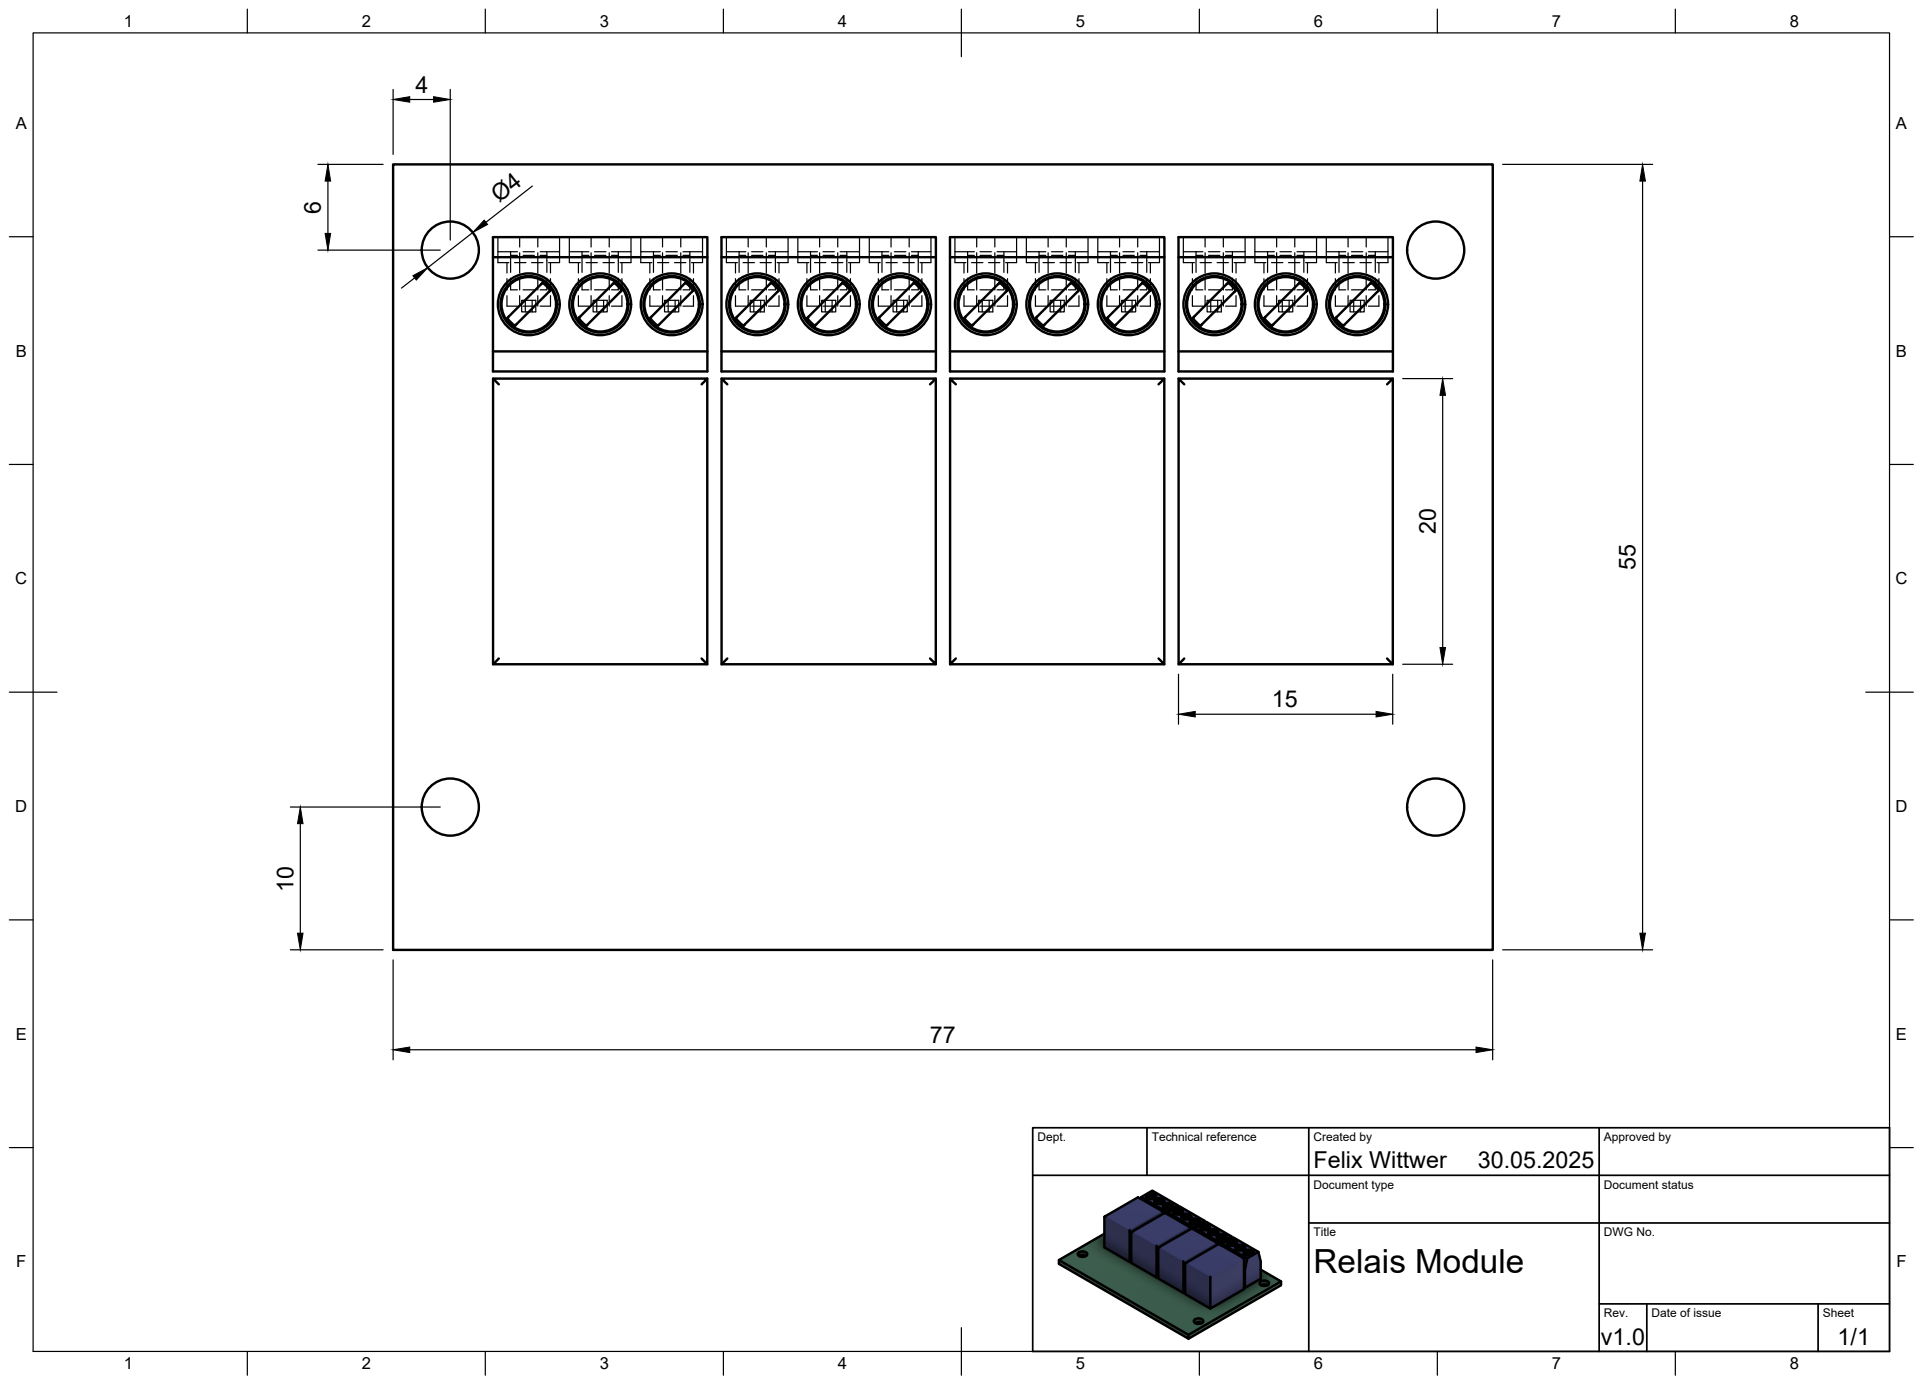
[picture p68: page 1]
Title; DWG No.; Rev.; Date of issue; Sheet; Relais Module

Dept. | Technical reference | Created by Felix Wittwer 30.05.2025 | Approved by

Document type | Document status

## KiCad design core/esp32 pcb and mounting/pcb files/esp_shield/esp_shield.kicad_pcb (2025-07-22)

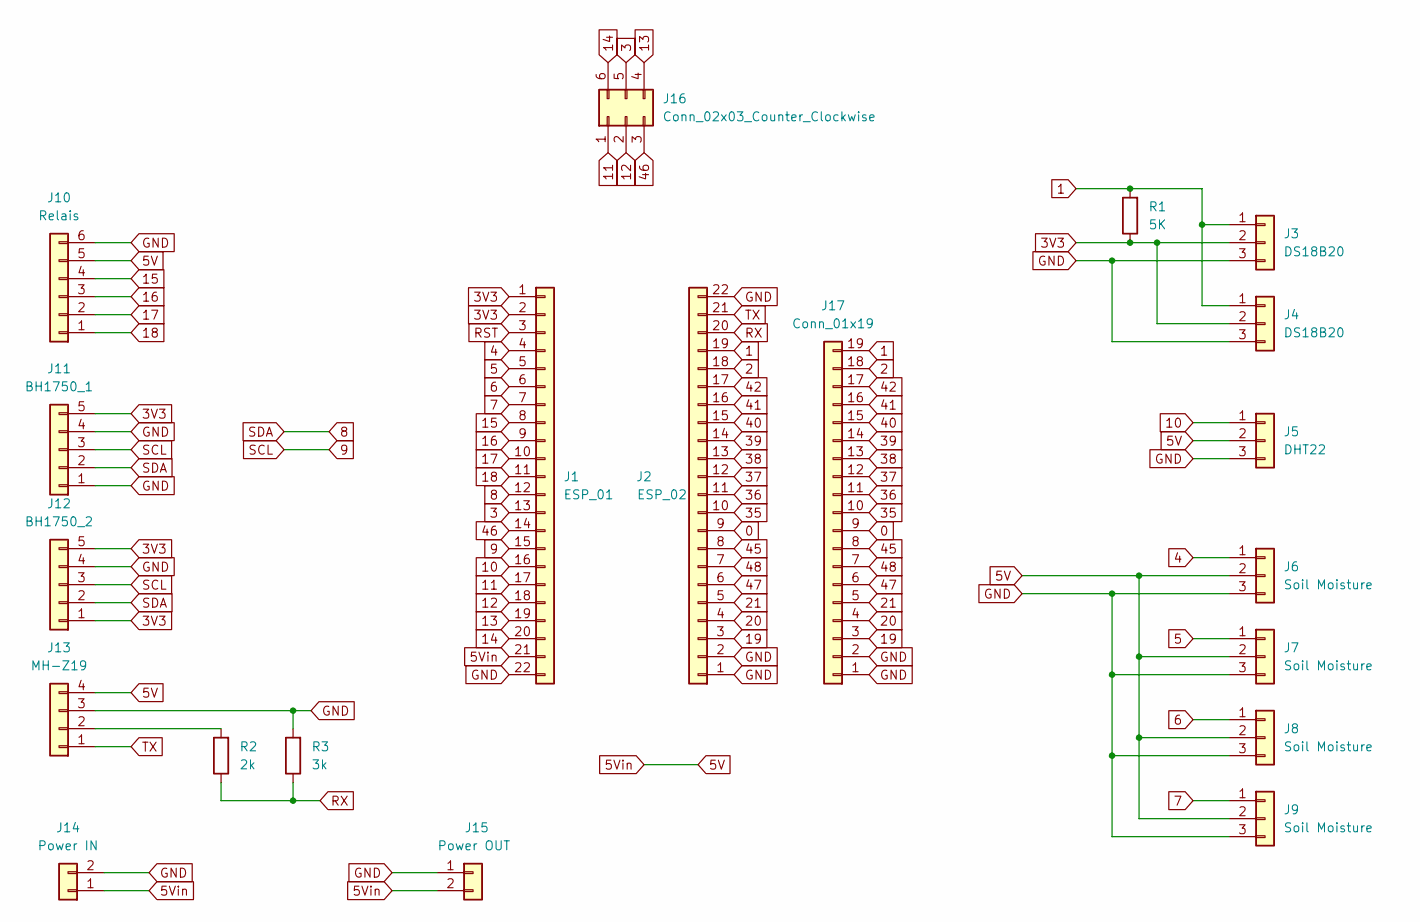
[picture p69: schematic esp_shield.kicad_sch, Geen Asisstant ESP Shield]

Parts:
J1: ESP_01; PinSocket_1x22_P2.54mm_Vertical
J2: ESP_02; PinSocket_1x22_P2.54mm_Vertical
J3, J4: DS18B20; TerminalBlock_Phoenix_MKDS-1,5-3-5.08_1x03_P5.08mm_Horizont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
J5: DHT22; TerminalBlock_Phoenix_MKDS-1,5-3-5.08_1x03_P5.08mm_Horizont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
J6, J7, J8, J9: Soil Moisture; TerminalBlock_Phoenix_MKDS-1,5-3-5.08_1x03_P5.08mm_Horizont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
J10: Relais; TerminalBlock_Phoenix_MKDS-1,5-6_1x06_P5.00mm_Horizontal
J11: BH1750_1; TerminalBlock_Phoenix_MKDS-1,5-5_1x05_P5.00mm_Horizontal
J12: BH1750_2; TerminalBlock_Phoenix_MKDS-1,5-5_1x05_P5.00mm_Horizontal
J13: MH-Z19; TerminalBlock_Phoenix_MKDS-1,5-4_1x04_P5.00mm_Horizontal
J14: Power IN; TerminalBlock_Phoenix_MKDS-1,5-2_1x02_P5.00mm_Horizontal
J15: Power OUT; TerminalBlock_Phoenix_MKDS-1,5-2_1x02_P5.00mm_Horizontal
J16: Conn_02x03_Counter_Clockwise; PinHeader_2x03_P2.54mm_Vertical
J17: Conn_01x19; PinHeader_1x19_P2.54mm_Vertical
R1: 5K; R_Axial_DIN0207_L6.3mm_D2.5mm_P10.16mm_Horizontal
R2: 2k; R_Axial_DIN0207_L6.3mm_D2.5mm_P10.16mm_Horizontal
R3: 3k; R_Axial_DIN0207_L6.3mm_D2.5mm_P10.16mm_Horizontal

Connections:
0: J2.9, J17.9
1: J2.19, J3.1, J4.1, J17.19, R1.2
2: J2.18, J17.18
3: J1.13, J16.5
3V3: J1.1, J1.2, J3.2, J4.2, J11.5, J12.1, J12.5, R1.1
4: J1.4, J6.1
5: J1.5, J7.1
5V: J1.21, J5.2, J6.2, J7.2, J8.2, J9.2, J10.5, J13.4, J14.1, J15.2
6: J1.6, J8.1
7: J1.7, J9.1
8: J1.12, J11.2, J12.2
9: J1.15, J11.3, J12.3
10: J1.16, J5.1
11: J1.17, J16.1
12: J1.18, J16.2
13: J1.19, J16.4
14: J1.20, J16.6
15: J1.8, J10.4
16: J1.9, J10.3
17: J1.10, J10.2
18: J1.11, J10.1
19: J2.3, J17.3
20: J2.4, J17.4
21: J2.5, J17.5
35: J2.10, J17.10
36: J2.11, J17.11
37: J2.12, J17.12
38: J2.13, J17.13
39: J2.14, J17.14
40: J2.15, J17.15
41: J2.16, J17.16
42: J2.17, J17.17
45: J2.8, J17.8
46: J1.14, J16.3
47: J2.6, J17.6
48: J2.7, J17.7
GND: J1.22, J2.1, J2.2, J2.22, J3.3, J4.3, J5.3, J6.3, J7.3, J8.3, J9.3, J10.6, J11.1, J11.4, J12.4, J13.3, J14.2, J15.1, J17.1, J17.2, R3.2
unnamed: J13.2, R2.2
RST: J1.3
RX: J2.20, R2.1, R3.1
TX: J2.21, J13.1

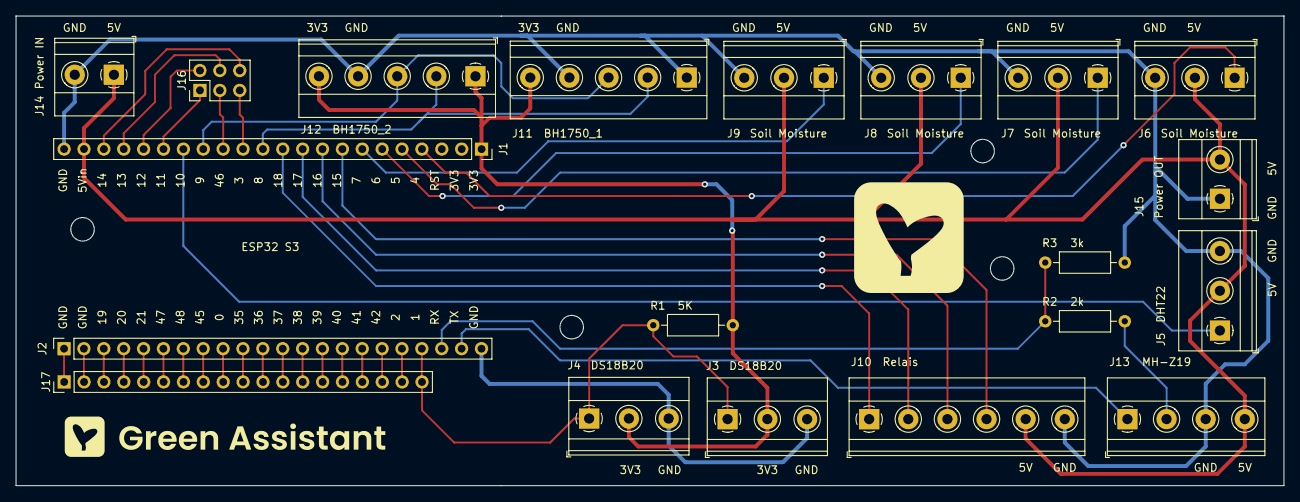
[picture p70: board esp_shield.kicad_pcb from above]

Board: 2 copper layers, 162.0 x 60.0 mm, 20 parts (0 on the bottom side), 40 nets.

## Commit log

2025-05-30 add core electrical box
    [core_electircal_box.f3z]
2025-05-30 add window contacts
    [window_magnet_bottom.stl, window_magnet_top.stl, window_reed_bottom.stl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]
2025-05-30 adding relais board inside action modules
2025-06-05 adding branding and ds18b20 sensor module
2025-06-23 add bh1750 light sensor module
    [bh1750_bottom.stl, bh1750_top.stl]
2025-06-23 improfing sensor moduel READMEs
2025-06-23 adding MH-Z19B sensor module
    [MH-Z19B mount bottom.stl, MH-Z19B mount top.stl]
2025-06-23 add DHT22 sensor module
2025-06-23 add soil moisture sensor module
2025-06-23 finishing off sensor modules
    [MH-Z19B mount.step, bh1750_case.step, window_contacts.step]
2025-06-24 adding esp32 pcb shield
    [esp_shield-B_Cu.gbr, esp_shield-B_Mask.gbr, esp_shield-B_Paste.gbr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]
2025-06-24 adding mount for pcb
    [pcb_mount.3mf, pcb_mount.step, pcb_mount.stl]
2025-06-25 adding mounting for relais
    [Relais Module mounting.3mf, Relais Module mounting.step, Relais Module mounting.stl]
2025-06-25 add irrigation system module
    [end-piece.step, end-piece.stl, nozzle-piece.step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]
2025-06-25 add new electrical box and wiring diagram
    [Eaton_Box_ci44x_125_na v20.f3z, core_electircal_box.f3z]
2025-06-30 adding BOM
    [BOM.csv, Hackclub_BOM.csv]
2025-06-30 making BOM readable for GitHub
    [BOM.csv]
2025-07-01 renaming folders for Hackclub
    [BOM.csv, Eaton_Box_ci44x_125_na v20.f3z, Hackclub_BOM.csv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]
2025-07-17 add cable clips
    [BOM.csv, Eaton_Box_ci44x_125_na v20.f3z, Eaton_Box_ci44x_125_na v20.step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]
2025-07-18 assemble pcb
2025-07-18 add M3 nut adapter
    [M3_nut_adapter.step, M3_nut_adapter.stl]
2025-07-19 add testing wiring to JOURNAL
2025-07-21 start wiring
2025-07-22 finish wiring + a small change on the pcb + start adding manual
    [esp_shield-B_Cu.gbr, esp_shield-B_Mask.gbr, esp_shield-B_Paste.gbr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]
2025-07-25 installing more sensors inside the greenhouse
2025-07-26 add more configuration for irrigation system - watering routine - helpers for manual watering - register buildin LED
2025-08-06 add new version of door and window sensors
    [door_magnet_holder.step, door_sensor_bottom.stl, door_sensor_top.stl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]
